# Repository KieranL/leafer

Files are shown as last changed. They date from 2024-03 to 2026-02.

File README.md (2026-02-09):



# Leafer

 A 3D printed RC snowmobile styled after machines from the 70s

Currently a work in progress and there is a very good chance files and BOM will change

[Download all files](https://github.com/KieranL/leafer/archive/refs/heads/main.zip)




##

Join the discord group https://discord.gg/C744rbBbvj

## BOM 

Electronics have been tested to work in this config unless noted

Note: some of these are affiliate links

- Motor (with matching esc)
  - NEW!!!! my new favourite combo with a D3536 750kv outrunner and Hobbywing 16BL30 ESC. Low CG, plenty of power, and no belt or aluminum/printed driveshaft needed. Works with either bulkhead type
    - [ESC Hobbywing 16BL30 v2](https://s.click.aliexpress.com/e/_c4OfwmCF)
    - [D3536 750kv outrunner](https://www.aliexpress.com/item/1005004728139495.html) (will need flat ground on to output shaft)
  - 380 size brushless motor, 19mm hole spacing (max 28mm diameter) ~3100kv
    - Expensive, nicer option [Rocket Supersonic sensored 380 3300kv](https://s.click.aliexpress.com/e/_DdVOuNJ)
    - Cheap option with servo [Rocket 2845 3100kv](https://www.aliexpress.com/item/1005001562382697.html)
  - 540/36xx size motors should work with a different frame (included)
- 2-3s LiPo 850-2200mah
  - 2200mah 2s gives around 25-30 minute run time in low snow/icy conditions with a 3300kv sensored 380 motor 
    - I run CNHL Black Series 1300-1500mah 2-3s batteries that fit well in the front. There is also room under the seat but I don't recommend putting the battery there
- Battery strap
- 6+ MR83 3x8x3 bearings 
  - 4 for rear idlers, 2 for front idler wheels and some for a belt tensioner if needed    
- 8x MR128 8x12x3.5 Bearings
  - 4x for the spindles, 2x for the driveshaft, 2x for the upper idler wheels
- 1/10 scale servo or 9g/TR4 servo
- 70-80mm shock
  - I use 70mm but if you want it to sit a littler higher 80mm works
- 48mm Mini E-Revo shocks for skis (Optional)
  - GPM ones work well [GPM shock](https://s.click.aliexpress.com/e/_c2y8ozYZ)
- 150g 85a TPU for track and hood hinge/straps
  - 95a may work but the track will not be nearly as flexible and take more power to turn
- 1kg rigid filament
  - PLA+/Tough PLA works well but most components it does not matter
- M2 Screws
  - 6-8mm long for the spindle covers and front bumper
- M2.5 Screws (if using ski shocks)
  -  2 10mm, 2 16mm
- M3 screws
  - Mostly 6mm, 8mm, 12mm, 16mm, and 25mm
- M3 Threaded rod
  - skid rear axle (75mm) and steering links (depends on servo setup)
- Motor drive pulley (not needed for direct drive setup)
  - 12t 2GT 3.175mm bore (or 5mm bore with shaft adapter) pulley for 380 motor
  - 16-20t 2GT 4-5mm bore pulley for 36XX
- Driven pulley (printable options will be included) (not needed for direct drive setup)
  - 58-64t for 380
  - 56-60t for 36XX
- 188mm long 6mm wide 2GT Closed loop belt (not needed for direct drive setup)
- short piece of gt2 belt for front limiter strap
- 8mm aluminum/steel driveshaft if not using the printed one
  - slightly shorter overall but the bolt spacing is the same as skeeride 2 shaft which will also fit (not needed for direct drive setup)
- Any 2+ channel radio system should work, I recommend one with a gyro
  - I am using the [Turbo Racing P52 transmitter with RX49 receiver](https://s.click.aliexpress.com/e/_c3DZknCp) since these recievers will pair with the OEM RTR Vanquish crawler radios
- Lights (optional)
  - https://s.click.aliexpress.com/e/_c3cogIUp these injora 17mm lights, take them out of the housing. headlight uses a pair, and the tail light plus dash light (wip) will each use a single pcb of the pair. So in total 2 sets of lights for the whole sled

## Printing

- Print the track, hood straps, hood hinges, snow flap, and spindle covers in TPU
- The spindles need to have really good layer adhesion so make sure to use a strong material and maybe bump up the hotend temp a bit
- Material choice for most other parts does not matter but the springs I would suggest PC-ABS or PLA+
- Some parts will need supports
  - the tunnel has integrated supports included

Note: The rear axle cross shaft and front cross brace look the same, but the rear one has a larger hole so you can slide a threaded rod through, where as the front is smaller so you can thread a bolt into it

## The build

### Skid

Glue the gt2 belt limiter strap into the tensioner, and wrap the other end around the front skid brace and lock it down with a zip tie




### Steering

There are 2 servo size options, both will work with option A

#### Option A

Printed steering link between each spindle, with a link made with m3 rod and ends from the servo horn to the printed link




#### Option B 

Only works with the smaller 9g/TR4 servo

Link between spindles with m3 rod and link from the servo to the right spindle




### Bellypan

The little tabs on the bellypan are to help align the hood, which requires carefully heating and bending the tabs upward so they stick out from the edges

https://github.com/user-attachments/assets/de6299b1-76f1-442c-9996-66a0bb9452ee

### Direct drive setup





### Ski



From top to bottom:
- saddle_upper or saddle_upper_spread
- helper_spring
- spring
- saddle_lower
- bump_stop

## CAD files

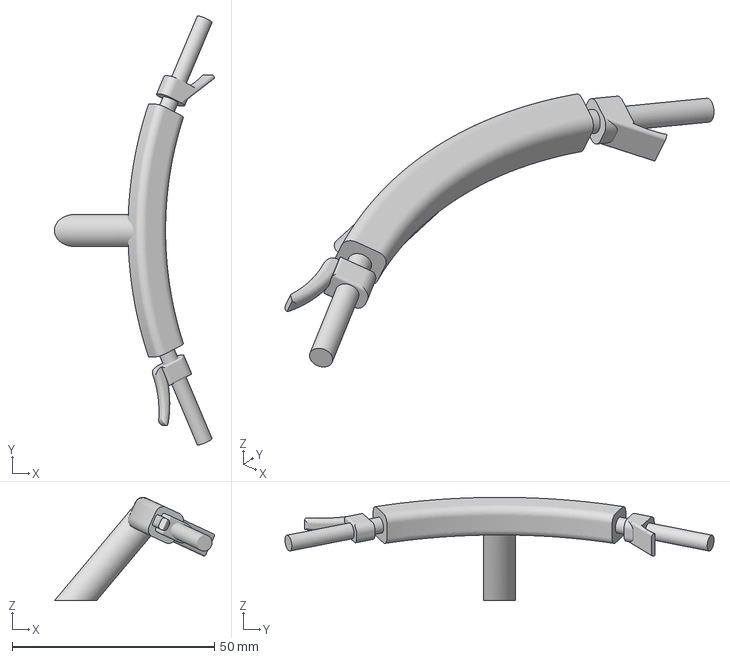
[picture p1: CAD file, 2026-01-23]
print files/body/handlebars.3mf
39.6 x 106.1 x 25.6 mm

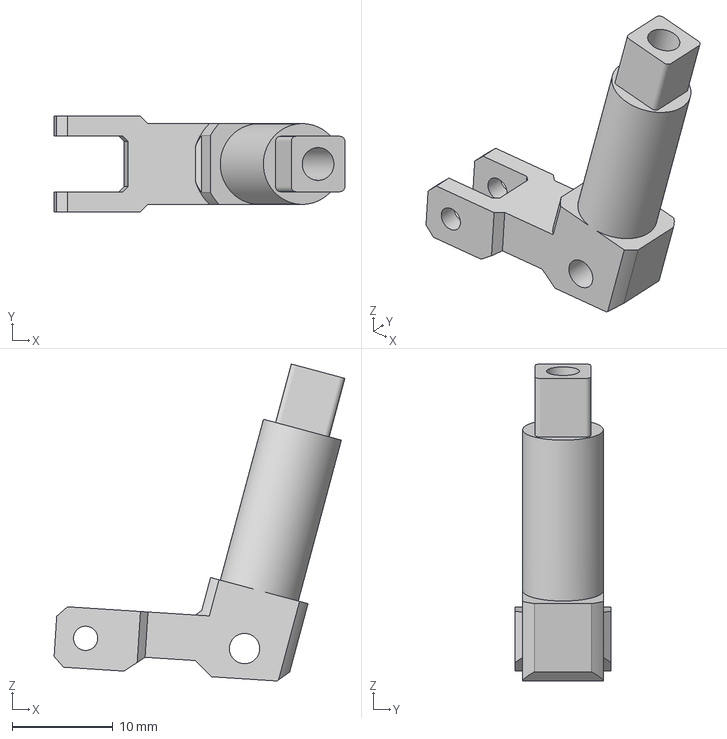
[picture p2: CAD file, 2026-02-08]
print files/chassis/Spindle_right.3mf
28.8 x 9.50 x 31.4 mm

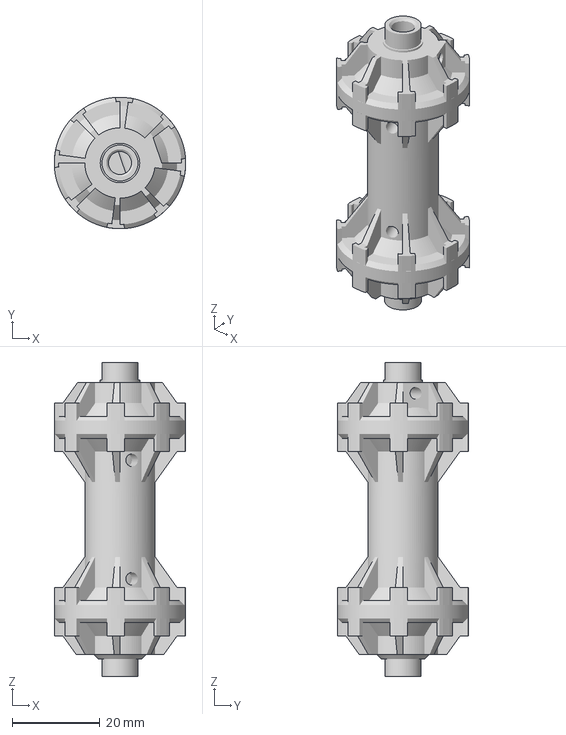
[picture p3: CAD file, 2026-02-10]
print files/drivetrain/Direct Drive Sprocket.3mf
29.9 x 29.9 x 71.5 mm

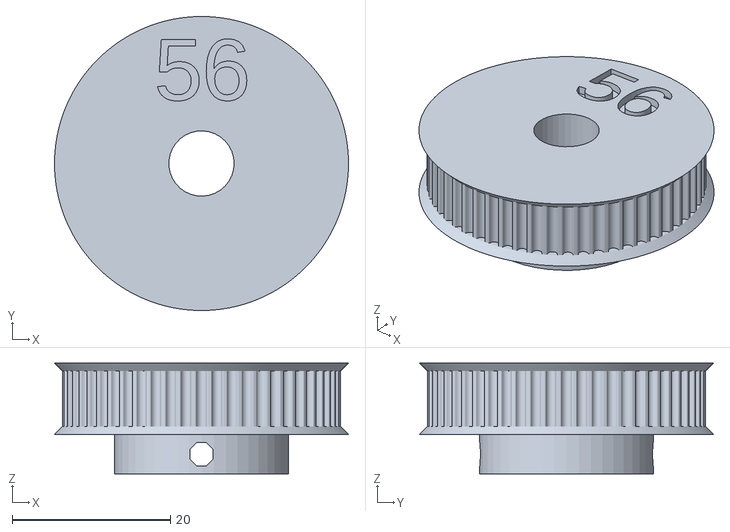
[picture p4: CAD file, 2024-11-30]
print files/drivetrain/Pulleys/Pulley_56t.stl
37.1 x 37.1 x 14.0

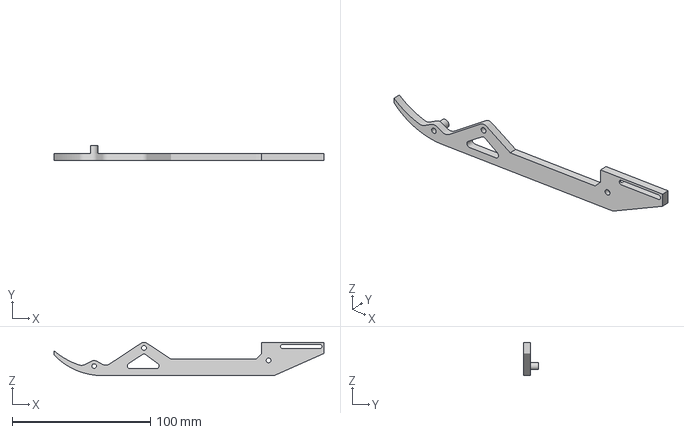
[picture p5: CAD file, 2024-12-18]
print files/skid/Rail_r.3mf
195.0 x 10.5 x 24.0 mm

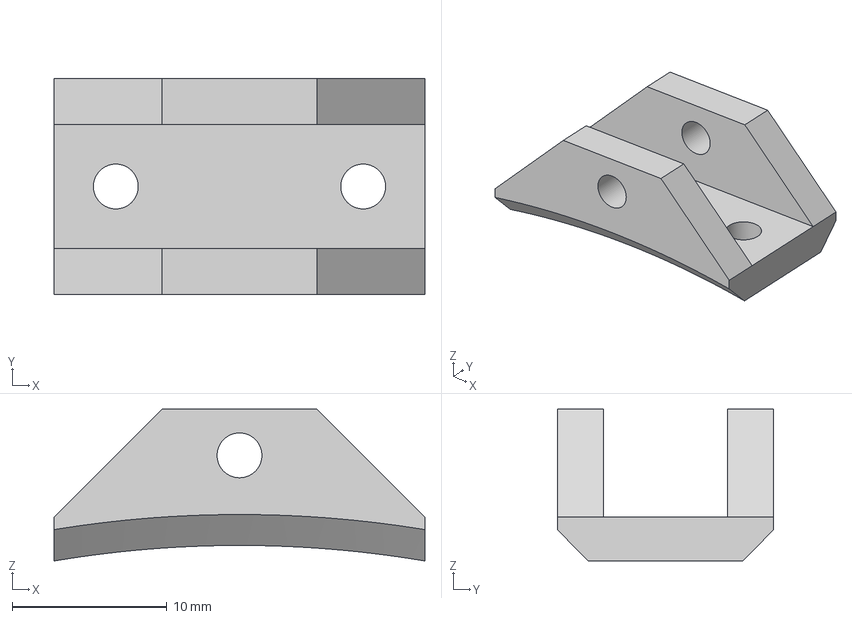
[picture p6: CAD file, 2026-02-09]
print files/skis/Saddle_upper.3mf
24.0 x 14.0 x 9.83 mm

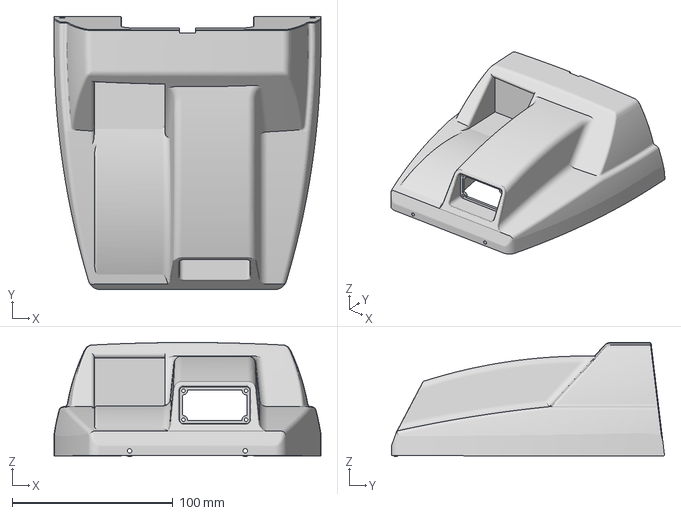
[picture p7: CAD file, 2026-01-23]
print files/body/Hood.3mf
166.0 x 169.9 x 71.0 mm

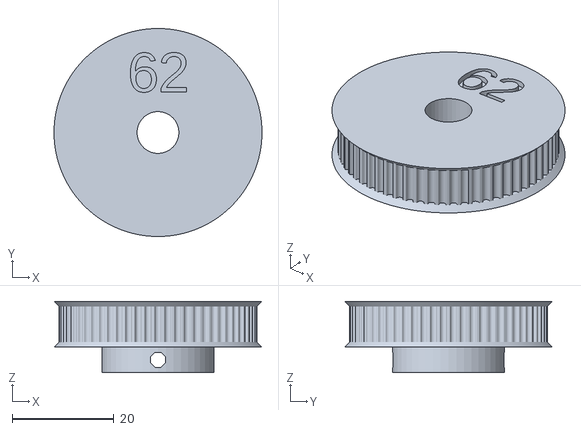
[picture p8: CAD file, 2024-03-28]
print files/drivetrain/Pulleys/Pulley_62t.stl
41.0 x 41.0 x 14.0

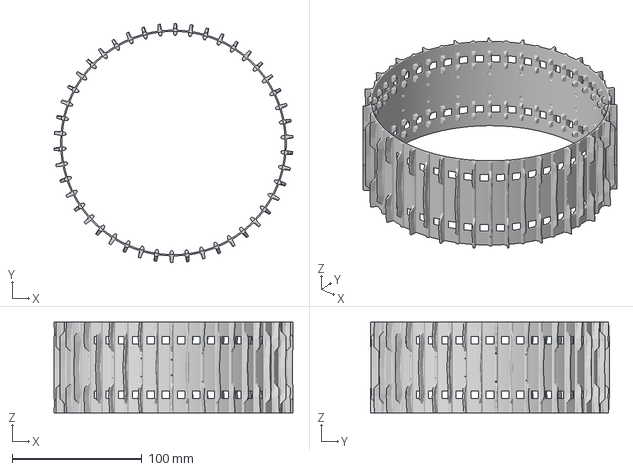
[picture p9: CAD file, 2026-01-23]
print files/drivetrain/track_116.3mf
184.2 x 184.4 x 70.0 mm

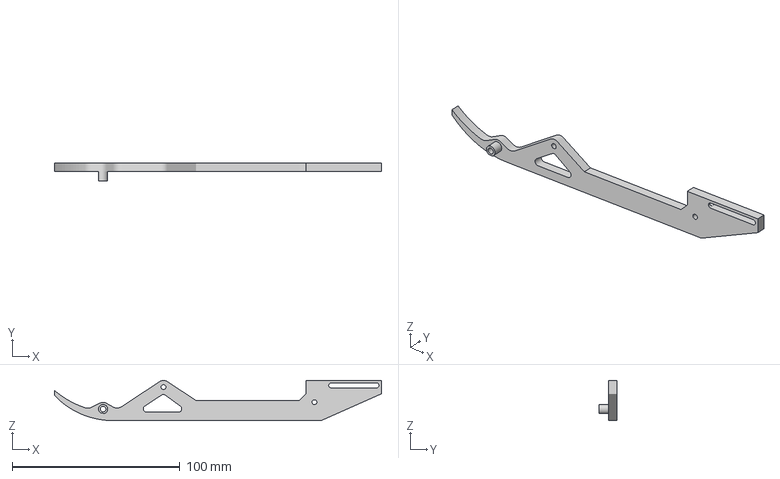
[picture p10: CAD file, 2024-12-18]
print files/skid/Rail_l.3mf
195.0 x 10.5 x 24.0 mm

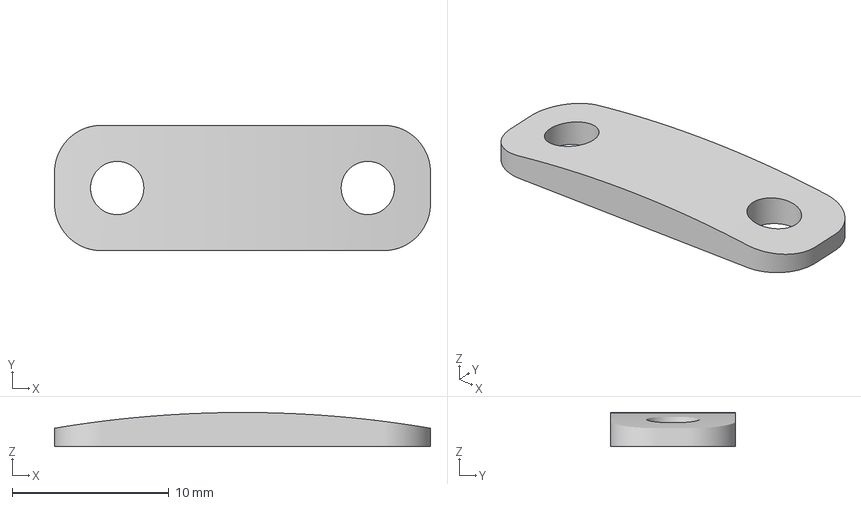
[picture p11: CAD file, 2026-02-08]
print files/skis/Saddle_lower.3mf
24.0 x 8.00 x 2.17 mm

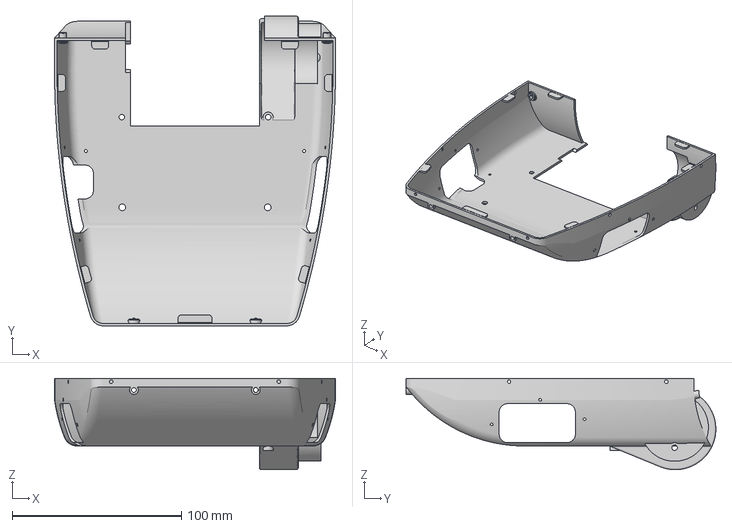
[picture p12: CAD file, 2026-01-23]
print files/body/Bellypan.3mf
166.0 x 183.0 x 54.0 mm

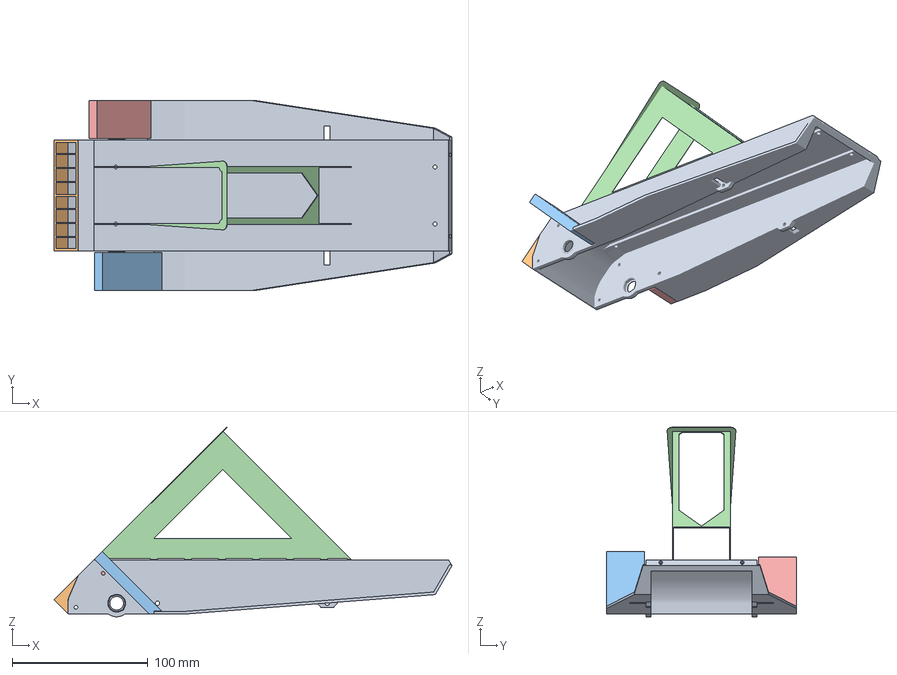
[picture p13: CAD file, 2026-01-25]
print files/chassis/Tunnel.3mf
293.0 x 140.0 x 139.6 mm
Tunnel
Tunnel_front_support
l_running_board_support
main_support
r_running_board_support

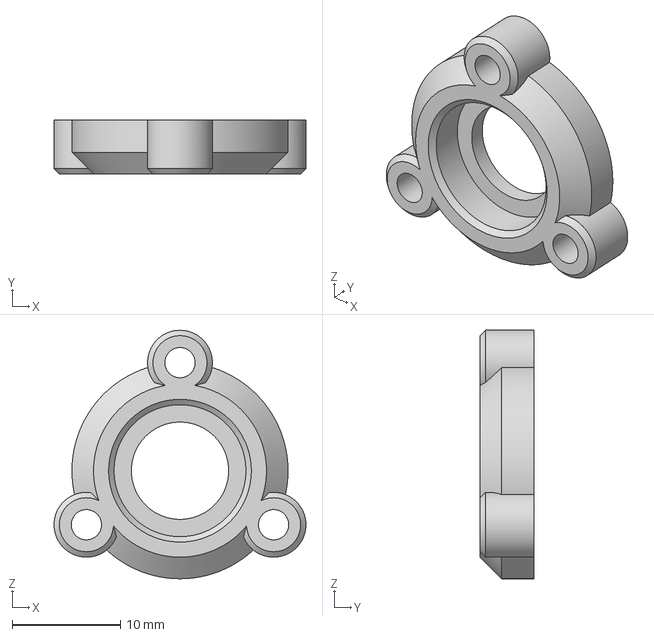
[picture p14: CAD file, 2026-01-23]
print files/drivetrain/direct_drive_drive_bearing_carrier.3mf
23.3 x 5.00 x 23.0 mm

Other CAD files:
print files/chassis/Spindle_left.3mf
print files/drivetrain/Pulleys/Pulley_68t.stl
print files/skid/Front_arm.3mf
print files/skis/Saddle_upper_spread.3mf
print files/body/Hinge.3mf
print files/body/Seat.3mf
print files/body/Snow_flap.3mf
print files/body/Strap.3mf
print files/body/Tank.3mf
print files/body/front_Bumper.3mf
print files/body/headlight_housing_front.3mf
print files/body/headlight_housing_rear.3mf
print files/body/headlight_lense.3mf
print files/body/rear_bumper.3mf
print files/body/spindle_cover.3mf
print files/body/tail_light_holder.3mf
print files/body/tail_light_lense.3mf
print files/chassis/Bulkhead_36mm_1_10.3mf
print files/chassis/Bulkhead_380_tr4.3mf
print files/chassis/steering_arm_left.3mf
print files/chassis/steering_arm_right.3mf
print files/chassis/steering_link.3mf
print files/chassis/tunnel_direct_drive.3mf
print files/drivetrain/Drive Sprocket.3mf
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

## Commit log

2024-03-19 fix bogie wheel mounting
2024-03-28 Upload pulleys
    [Pulley_58t.stl, Pulley_59t.stl, Pulley_60t.stl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]
2024-11-03 BOM updates
2024-11-30 first release???
    [Bellypan.3mf, Bulkhead_36mm_1_10.3mf, Bulkhead_36mm_tr4.3mf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]
2024-12-06 thicker hinge
    [Hinge.3mf]
2024-12-18 add rails
    [Rail_l.3mf, Rail_r.3mf]
2024-12-23 update cad
2024-12-24 new experimental track, a little thinner so it turns easier and new lug design for better traction on hard surfaces
    [track_116_experimental.3mf]
2025-01-01 modify holes for hood strap and hinge
    beef it up a bit
    [Bellypan.3mf, Hood.3mf]
2025-01-15 add v2 of experimental track
    [track_116_experimental_solid_cross_bars.3mf]
2025-12-15 add hood with headlight and seat with tail light
    [Hood.3mf, Seat.3mf, headlight_housing_front.3mf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]
2026-01-23 Add direct drive setup and other improvements
    [Bellypan.3mf, Bulkhead_36mm_1_10.3mf, Bulkhead_36mm_tr4.3mf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]
2026-01-25 fix missing support
    [Tunnel.3mf, tunnel_direct_drive.3mf]
2026-02-08 add saddle lower
    [Saddle_lower.3mf, Spindle_left.3mf, Spindle_right.3mf]
2026-02-09 upload updated saddle upper for new style shock mount
    [Saddle_upper.3mf]
2026-02-09 update bearing info
2026-02-10 fix missing feature on direct drive sprocket
    [Direct Drive Sprocket.3mf]
